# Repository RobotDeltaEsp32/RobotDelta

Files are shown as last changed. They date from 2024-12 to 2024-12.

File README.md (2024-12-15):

# RobotDelta
Este repositorio contiene el diseño y documentación completa de un robot delta desarrollado en un proyecto académico. Se realizaron cálculos de cinemática directa e inversa, simulaciones estructurales y análisis del espacio de trabajo. El control se implementó con ESP32, capturando posiciones angulares y validando con pruebas experimentales.

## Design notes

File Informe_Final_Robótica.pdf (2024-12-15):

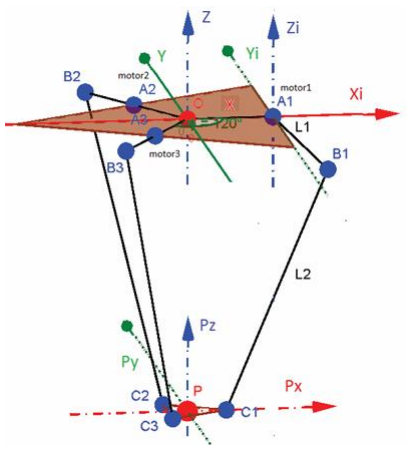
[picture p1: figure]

### Departamento de Ingeniería Mecatrónica Robótica (IMT-342) / Informe Final @ 2024 Universidad Católica Boliviana “San Pablo” – Santa Cruz

# Diseño de Robot Delta

Roberto Carlos Escobar Salcedo 8vo Semestre
roberto.escobar@ucb.edu.bo

Resumen — Este proyecto presenta el diseño, construcción y control de un robot delta, en el cual se llevaron a cabo cálculos de cinemática directa e inversa para determinar posiciones y ángulos articulares. Se realizaron simulaciones estructurales, incluyendo análisis de tensión nodal, desplazamiento estático y deformación unitaria para evaluar el comportamiento mecánico del robot. Se realizó el análisis del espacio de trabajo de este robot y se identificaron sus rangos de movimiento. El control de este robot se realizó mediante la placa ESP32 que se encargó de la captura de datos de la posición angular de los motores y de su movimiento. El proceso incluyó el diseño estructural, la selección de materiales y componentes, y la implementación de pruebas experimentales para validar el comportamiento del sistema mediante la comparación entre valores teóricos y mediciones de los valores reales.

Palabras clave: Robot delta, SCP32, Cinemática inversa, Cinemática directa, servomotores.

Abstract — This project presents the design, construction and control of a delta robot, in which forward and inverse kinematics calculations were carried out to determine joint positions and angles. Structural simulations were performed, including nodal stress analysis, static displacement and unitary deformation to evaluate the mechanical behavior of the robot. The workspace of this robot was analyzed, and its ranges of motion were identified. The control of this robot was carried out by the ESP32 board that was responsible for capturing data on the angular position of the motors and their movement. The process included the structural design, the selection of materials and components, and the implementation of experimental tests to validate the behavior of the system by comparing theoretical values with measurements of the real values.
I. INTRODUCCIÓN

La robótica ha avanzado considerablemente en los últimos años, impulsada por la necesidad de optimizar procesos en industrias que requieren rapidez, precisión y eficiencia. En este contexto, los robots delta han emergido como una solución ideal en tareas de alta velocidad y precisión, especialmente en industrias como la alimentaria, farmacéutica y electrónica, donde el manejo de objetos ligeros es crucial. Diseñado inicialmente por el Dr. Reymond Clavel, el robot delta se distingue por su arquitectura paralela, la cual permite una manipulación rápida y precisa de objetos, minimizando la inercia debido a su diseño liviano y simplificado [1].

Los robots delta utilizan tres brazos articulados que convergen en una plataforma móvil, lo que les permite alcanzar velocidades y aceleraciones superiores a las de robots con arquitecturas seriales. Este diseño ofrece además una ventaja significativa en cuanto a rigidez y precisión, lo que facilita aplicaciones de manipulación en las que se requieren altos niveles de repetibilidad [2]. Estas características han impulsado el uso de los robots delta en el ámbito industrial y en la investigación, donde la tendencia actual es integrar sensores avanzados y sistemas de visión para mejorar la precisión en entornos complejos [3].

Con lo mencionado líneas arriba este proyecto plantea el desarrollo de un robot delta para esto de debe: Obtener la cinemática directa e inversa del robot delta, realizar el dimensionamiento de los motores, diseñar la estructura en SolidWorks y comprobar funcionamiento del robot.

II. GEOMETRIA DEL ROBOT

El sistema de coordenadas inercial del robot delta se encuentra en un punto O en la base donde están ubicados los tres motores. El eje Z de este sistema de coordenadas es perpendicular a la base y el eje X perpendicular al eje del motor número 1.

Figura 1. Representación geométrica del robot delta

Sebastian Osorio Ferrufino 8vo Semestre
sebastian.osorio@ucb.edu.bo

Matías adorno Mazocato
8vo Semestre
matias.adorno@ucb.edu.bo

Jose Jesus Cabrera Pantoja Robótica IMT-342
Departamento ingeniería mecatrónica

En la Figura 1 se puede observar que cada motor tiene un brazo móvil conformado por dos eslabones, cuyas distancias son L1 y L2, las cuales son las mismas para cada brazo de cada motor. Cada motor se une al eslabón L1 por medio de una unión Ai, siendo un valor de i por cada motor (i=1, 2, 3). Los eslabones L1 y L2 se conectan mediante una unión Bi, y el eslabón L2 se une con una base móvil cuyo punto medio es el efector final P, esta unión de L2 con P se representa como Ci.

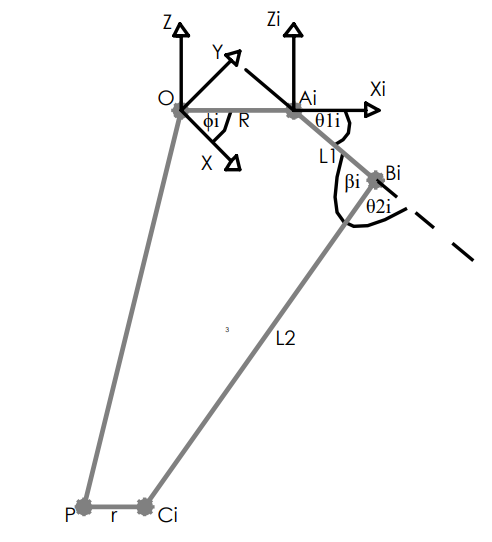
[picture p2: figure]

Figura 2. Sistemas de coordenadas y ángulos del robot delta

Cada brazo se encuentra sobre un sistema de coordenadas distinto al sistema de coordenadas inercial en el punto O, estos sistemas de coordenadas se encuentran a una distancia R con respecto al sistema de coordenadas inercial y con una rotación de un ángulo ϕi, siendo este 0°, 120° y 240° para los motores 1, 2 y 3 respectivamente, debido a que se debe tener una separación angular igual entre cada motor. Se tiene un ángulo θ1i entre el eje Xi y el vector ABi

̅̅̅, el cual es el ángulo que giran los motores, y otor ángulo θ1i entre la proyección del vector ABi

̅̅̅
y el eslabón L2. De igual manera, se tiene un ángulo interno β1i entre los eslabones L1 y L2.

Para conocer los vectores generados entre el punto inicial O y cada punto de unión se utiliza el método de la matriz de transformación, el cual representa la orientación y posición de un sistema de coordenadas rotado y trasladado respecto a otro.

OAi

̅̅̅̅̅ = [

C∅i | −S∅i | 0 RC∅i
S∅i | C∅i | 0 RS∅i
0 | 0 | 1 | 0
0 | 0 | 0 | 1

] [

0
0

0/1] = [

RC∅i
RS∅i
0
1

] Ec. 1

OBi

̅̅̅̅ = [

C∅i | −S∅i | 0 RC∅i
S∅i | C∅i | 0 RS∅i
0 | 0 | 1 | 0
0 | 0 | 0 | 1

] [

L1Cθ1i
0
−L1Sθ1i
1

] = [

C∅i

(L1Cθ1i + R)
S∅i

(L1Cθ1i + R)
−L1Sθ1i
1

] Ec. 2

OCi

̅̅̅ = [

C∅i | −S∅i | 0 RC∅i
S∅i | C∅i | 0 RS∅i
0 | 0 | 1 | 0
0 | 0 | 0 | 1

] [

PxC∅i + PyS∅i + r − R
PyC∅i − PxS∅i
Pz
1

] = [

Px + rC∅i
Py + rS∅i
Pz
1

] Ec. 3

Con las ecuaciones 1, 2 y 3 se obtienen los vectores BAi

̅̅̅̅̅,
BCi

̅̅ y ACi

̅̅.

BAi

̅̅̅̅̅ = OAi

̅̅̅̅̅ − OBi

̅̅̅̅̅ = [

−C∅iL1Cθ1i
−C∅iL1Cθ1i
L1Sθ1i
] | Ec. 4

BCi

̅̅ = OCi

̅̅̅̅ − OBi

̅̅̅̅̅ = [
Px − C∅i

(R + L1Cθ1i − r)
Py − S∅i

(R + L1Cθ1i − r)
Pz + L1Sθ1i

] Ec. 5

ACi

̅̅ = OCi

̅̅̅̅ − OAi

̅̅̅̅̅ = [
Px − C∅i

(r − R)
Py − S∅i

(r − R)
Pz

] Ec. 6

III. CINEMATICA INVERSA

La cinemática inversa permite encontrar los ángulos de entrada θ1i de cada motor a partir de conocer la posición P del efector final. Para esto se puede observar al robot de la siguiente manera:

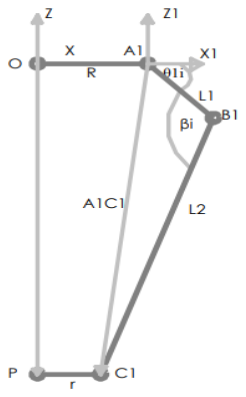
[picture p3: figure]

Figura 3. Representación trigonométrica del robot delta

En la Figura 3 se puede observar que se forma un triángulo entres los puntos Ai, Bi y Ci y se aplica teorema de cosenos para hallar la longitud de ACi

̅̅.

AC1

2 = L1

2 + L2

2 − 2L1L2 cos(βi
) | Ec. 7

Se calcula el coseno del ángulo utilizando la ecuación del producto escalar:

BAi

̅̅̅̅̅ ∗ BCi

̅̅ = |BA|
i

|BC|
i cos(βi
) | Ec. 8

Dado que L1 es la unión de los puntos A y B, y de igual manera, L2 es la unión de los puntos B y C, se tiene que:
L1 = |BA|
i | Ec. 9

L2 = |BC|
i | Ec. 10

Se reemplazan las ecuaciones 9 y 10 en la ecuación 8 y se obtiene:

cos(βi

) =

BAi

̅̅̅̅̅ ∗ BCi

̅̅
L1L2

Ec. 11

Se reemplaza la ecuación 11 en la ecuación 7:

AC1

2 = L1

2 + L2

2 − 2(BAi

̅̅̅̅̅ ∗ BCi

̅̅) | Ec. 12

Reemplazando los valores de las ecuaciones 5 y 4 en la ecuación 12:

AC1

2 = L1

2 − L2

2 + 2L1Cθ1i(PxC∅i + PyS∅i + r − R) − 2L1Sθ1iPz Ec. 13

Se tiene que la magnitud del vector ACi

̅̅ según la ecuación
6 es:

|AC|1 = AC1

2 = (Px + C∅i
(r − R))

2
+ (Py + S∅i

(r − R))

2
+ Pz … Ec. 14

Igualando las ecuaciones 13 y 14 se obtiene:

aiSθ1i + biCθ1i = ci | Ec. 15

Donde:

ai = −2PzL1 | Ec. 16
bi = 2L1(PxC∅i + PyS∅i + r − R) | Ec. 17

ci = (Px + C∅i

(r − R))

2
+ (Py + S∅i

(r − R))

2
+ Pz

2 + L1

2L2

2 Ec. 18

Utilizando identidades trigonométricas en la ecuación 15 se obtiene:

aiSθ1i + biCθ1i = √ai
2 + bi

2

∗ sin (θ1i + tan⁻¹ (

bi
ai

)) Ec. 19

Se igualan las ecuaciones 15 y 19, y se procede a despejar el ángulo de rotación de los motores:

θ1i = sin⁻¹
(

ci
√ai
2 + bi

2

)

− tan⁻¹ (

bi
ai

) Ec. 20

IV. CINEMATICA DIRECTA

La cinemática directa permite encontrar la posición P del efector final a partir del conocimiento de los ángulos de la posición de los motores.

A partir de la ecuación 5, que representa el punto de conexión del brazo con el efector final, se tiene que su magnitud es igual a L2, por lo cual se tiene que:

|BC|
i = L2

2 = (Px − C∅i
(R + L1Cθ1i − r))

2
+
(Py − S∅i

(R + L1Cθ1i − r))

2
+ (Pz + L1 + Sθ1i

)

2 Ec. 21

A partir de la ecuación 21 se realiza un sistema de ecuaciones reemplazando las 3 posiciones angulares de ϕi por cada motor, siendo estas 0°, 120° y 240° para los motores 1, 2 y 3 respectivamente.

{

(Px − R − L1cCθ11 + r)

2 + Py

2 + (Pzz + L11Sθ11)

2 = L2

2

(Px +
1
2

(R + L1Cθ12 − r))

2

+ (Py −
√3
2

(R + L1Cθ12 − r))

2
+ (Pz + L1Sθ12)

2 = L2

2

(Px +
1
2

(R + L1Cθ13 − r))

2

+ (PY +
√3
2

(R + L1Cθ13 − r))

2
+ (Pz + L1Sθ13)

2 = L2

2

Ec. 22

V. ESPACIO DE TRABAJO

El espacio de trabajo de un robot define la región tridimensional donde su efector final puede operar, teniendo en cuenta las limitaciones mecánicas, cinemáticas y estructurales. Para un robot delta, este espacio está influenciado por la geometría de los brazos, las restricciones de los actuadores y el rango angular de las articulaciones. Además, dentro de este espacio general, se encuentra el espacio de trabajo efectivo, que representa la región donde el robot puede operar de manera óptima y segura. Evaluar estas regiones es crucial para determinar la capacidad y alcance del robot en tareas específicas.

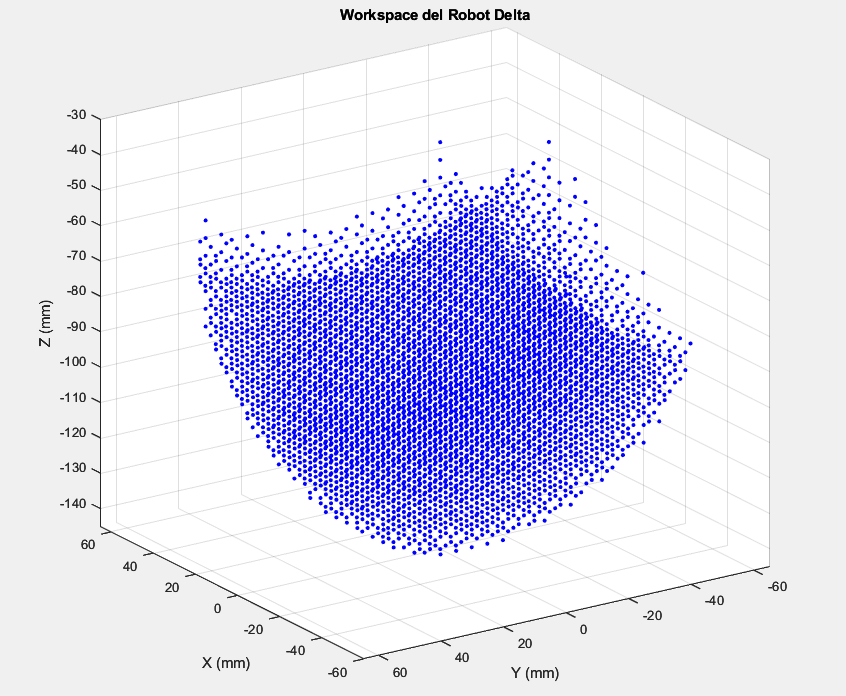
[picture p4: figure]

Figura 4. Espacio de trabajo robot delta.

Esta figura muestra el espacio de trabajo total del robot delta, representado como un conjunto de puntos en un sistema tridimensional. Cada punto corresponde a una posición alcanzable por el efector final del robot, considerando todas las configuraciones posibles. La forma generada refleja las restricciones geométricas y mecánicas del sistema, destacando las áreas donde el robot tiene mayor accesibilidad.

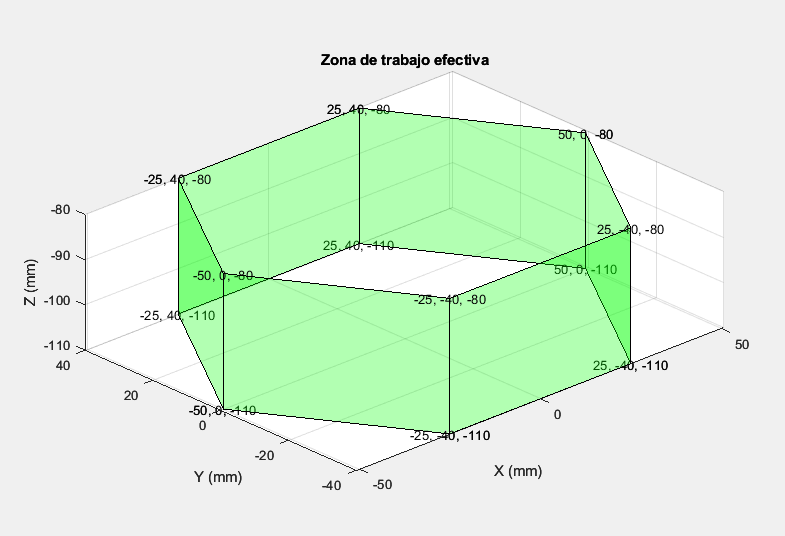
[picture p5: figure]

Figura 5. Espacio de trabajo efectivo robot delta

Aquí se representa el espacio de trabajo efectivo, una subregión dentro del espacio total donde el robot puede operar de forma segura y eficiente. Esta región está delimitada por factores como límites de velocidad, carga y precisión requerida. La figura utiliza una superficie verde para identificar claramente esta zona, resaltando las posiciones útiles y prácticas del efector final.

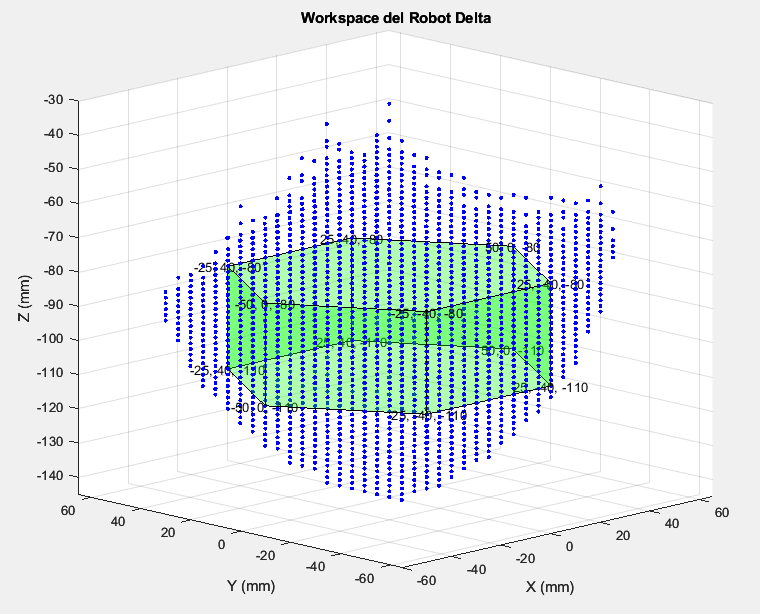
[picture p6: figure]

Figura 6. Espacio de trabajo efectivo en el espacio de trabajo total.

En esta figura se superpone el espacio de trabajo efectivo (en verde) dentro del espacio de trabajo completo (en azul). Esta representación combinada permite visualizar la relación entre ambas regiones, mostrando cómo el espacio efectivo ocupa solo una porción del espacio total. Esto es útil para identificar posibles áreas de operación óptima y para ajustar las tareas del robot a sus capacidades reales.

VI. REQUERIMIENTOS

Se presenta una tabla que muestra los requerimientos que debe cumplir el robot delta que se ha diseñado. Estos requerimientos se obtuvieron mediante el análisis de las especificaciones técnicas de los motores paso a paso utilizados, del análisis estructural y del cálculo del espacio de trabajo.

Tabla 1. Requerimientos

Requerimientos | Valores
Velocidad máxima | 300 RPM
Rango de movimiento motores | 0 a 90°
Carga máxima | 750g

VII. DISEÑO DE LA ESTRUCTURA

El proceso de diseño de la estructura del robot delta se desarrolló de manera iterativa, comenzando con la base superior, la cual se definió con una geometría triangular y lados redondeados, asegurando un soporte adecuado para los motores y los brazos. Posteriormente, se diseñó la base intermedia, con cortes rectangulares en los vértices para permitir el encaje con las patas y garantizar estabilidad. Las patas fueron diseñadas en MDF de 3 mm de grosor, con una longitud de 200 mm y segillas de 10 mm en los extremos, facilitando un ensamblaje firme con la base intermedia. Finalmente, se integraron componentes como el efector final, los brazos y los eslabones, fabricados en PLA mediante impresión 3D, asegurando precisión en las articulaciones y funcionalidad en el movimiento del robot.

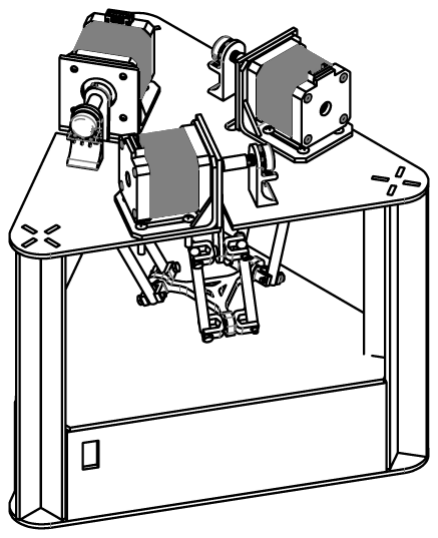
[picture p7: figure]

Figura 7. Robot delta

El criterio principal para el diseño fue la optimización de materiales y la facilidad de manufactura, utilizando MDF y PLA debido a su disponibilidad y facilidad de corte o impresión. Además, se priorizó la estabilidad estructural y el ensamblaje eficiente, garantizando que todas las piezas encajaran de forma precisa para soportar los esfuerzos durante la operación. Las dimensiones y detalles específicos, como las perforaciones para motores y las ranuras de encaje, se ajustaron para cumplir con los requisitos de funcionalidad y precisión del robot delta.

Los criterios de selección y diseño de piezas se han basado en tres factores principales: disponibilidad, costos y tiempos. La disponibilidad ha sido el criterio más importante, ya que representa la capacidad de acceder a cada componente de manera oportuna para evitar retrasos en el ensamblaje. Los costos también se han considerado cuidadosamente para mantener el proyecto dentro del presupuesto asignado, sin comprometer la funcionalidad y resistencia del robot. Además, los tiempos de armado y fabricación han sido cruciales debido a la restricción temporal del proyecto, buscando métodos de fabricación rápidos para la mayoría de las piezas y reservando métodos más complejos para los componentes que lo requieran específicamente. Estos criterios han sido clave para lograr un diseño efectivo y funcional, adaptado tanto al presupuesto como a la restricción temporal del proyecto.

VIII. SIMULACION DE ESFUERZOS

La simulación de esfuerzos es una herramienta fundamental en el diseño de sistemas mecánicos, ya que permite evaluar cómo se comportan los componentes bajo diversas condiciones de carga. A través de este análisis, es posible identificar zonas críticas de tensión, desplazamiento y deformación, garantizando así la fiabilidad y seguridad del diseño. En este caso, se realizó un análisis estático del robot delta, enfocándose en los brazos y los componentes principales, para evaluar su comportamiento estructural.

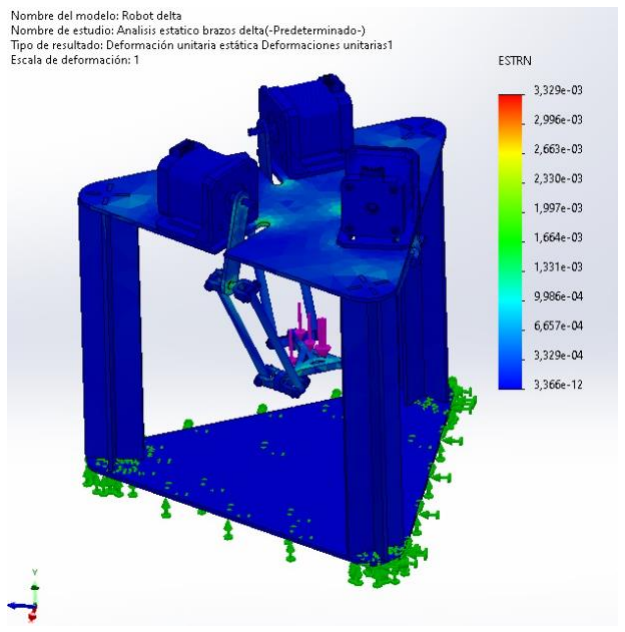
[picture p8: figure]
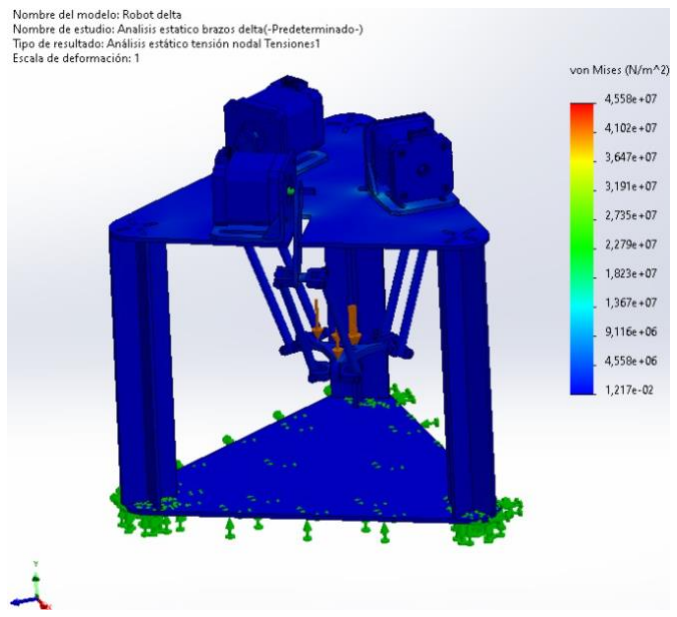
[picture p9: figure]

Figura 8. Simulación tensión nodal.

Esta simulación muestra la distribución de tensiones von Mises en el robot delta bajo una carga específica. Los colores representan los niveles de tensión, desde azul (baja tensión) hasta rojo (alta tensión). Las zonas más críticas se identifican en las áreas rojas, donde el material podría estar más cerca de su límite elástico. Esto permite evaluar la resistencia de los materiales en las partes más exigidas.

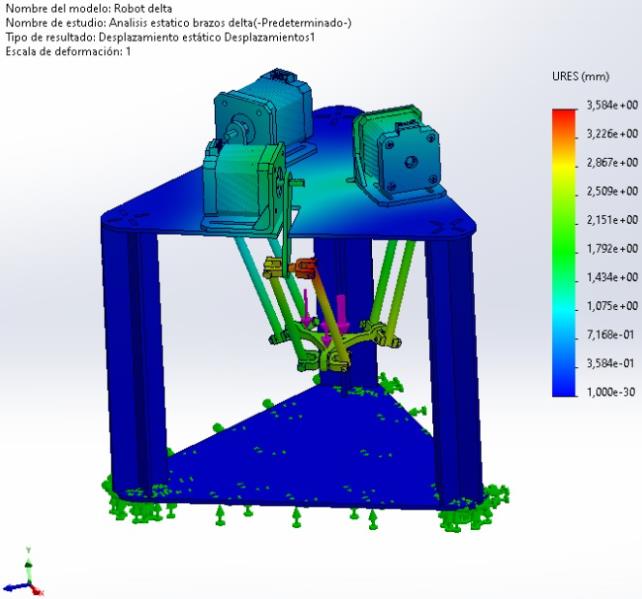
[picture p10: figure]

Figura 9. Simulación desplazamiento estático.

En este análisis, se presenta el desplazamiento total en cada nodo del robot delta. Los colores van desde azul (mínimo desplazamiento) hasta rojo (máximo desplazamiento). Este resultado es clave para entender cómo las fuerzas aplicadas afectan la estabilidad y precisión del sistema, ya que
desplazamientos | excesivos | pueden | comprometer | el
rendimiento del robot.

Figura 10. Simulación deformación unitaria estática.

La simulación muestra la deformación unitaria de los componentes del robot delta. Los colores indican la magnitud de la deformación, desde azul (mínima deformación) hasta rojo (máxima deformación). Este análisis permite verificar si las deformaciones son aceptables dentro de los límites de diseño, garantizando que no se produzcan fallos por deformación excesiva.
IX. SELECCIÓN DE MATERIALES Y COMPONENTES
A. Motor

Se ha seleccionado el motor NEMA 16, un motor paso a paso, debido a su capacidad para controlar con precisión los ángulos de los brazos del robot, lo cual es crucial para el movimiento del efector final. Este motor cuenta con un torque máximo de 1.2 kg·cm, lo que se ha evaluado como suficiente para soportar la carga requerida de 2 kg, considerando la distribución del esfuerzo entre los tres motores y la geometría del sistema. Con una longitud de eslabón de 6 cm, la fuerza máxima que cada motor puede generar se ha calculado como F =

T
d

=

1.2kg⋅cm
6cm

, resultando en una capacidad de carga de aproximadamente 0.2 kg por motor a esa distancia. Al estar distribuidos los 0.5 kg entre los tres motores, cada uno soporta una carga de aproximadamente 0.2 kg, lo que se encuentra dentro de su capacidad operativa.

Esta selección también se ha fundamentado en la disponibilidad del motor como recurso proporcionado por la universidad, lo que ha permitido su integración sin costos adicionales ni retrasos en la adquisición. Además, la naturaleza precisa y controlable de los motores NEMA 16 ha sido ideal para garantizar la estabilidad y el desempeño del efector final, validando su inclusión como componente clave en el diseño del robot delta.

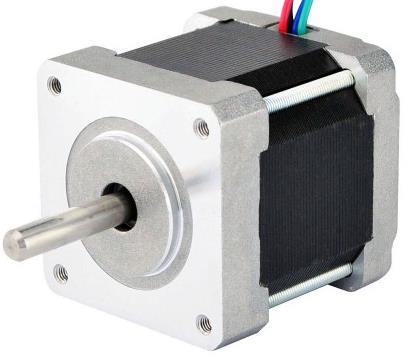
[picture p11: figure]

Figura 11. Nema 17.

B. Base del motor

Se ha decidido utilizar una base en forma de "L" para el motor NEMA 17, con el propósito de reducir los tiempos de fabricación, evitando el proceso de impresión de una base personalizada. La forma en "L" ha permitido fijar el motor de manera estable sobre la cara superior de la base estructural, asegurando una alineación adecuada en el montaje. Aunque la base específica para el NEMA 16 no se encontraba disponible, se optó por la del NEMA 17 debido a que, a pesar de ser ligeramente más grande, comparte el mismo tamaño y posición de tornillos, permitiendo su compatibilidad sin afectar la estabilidad o funcionalidad del sistema.

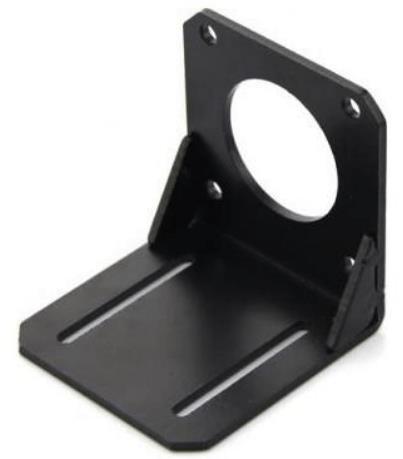
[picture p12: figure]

Figura 12. Base del motor Nema 17.

X. DISEÑO DE ESTRUCTURA
A. Base superior

El diseño de la base superior se ha realizado en una estructura triangular con lados redondeados, con una distancia de 85 mm desde el centro hasta cada arista y bordes con un radio de 20 mm. Cada cara cuenta con un corte central de 4 mm de grosor y 50 mm de longitud, terminando en un redondeado de 4 mm de radio. En cada vértice se han integrado ranuras rectangulares de 3 mm por 10 mm para fijar las patas, organizadas en forma de cruz con una separación de 10 mm entre las ranuras colineales y orientadas hacia el centro. La pieza, con un grosor uniforme de 3 mm, ha sido cortada a partir de una lámina de madera mediante una cortadora láser, logrando bordes precisos y uniformes. Este diseño ha proporcionado una base estable y alineada, con perforaciones para los motores y aperturas que garantizan el movimiento sin obstrucciones de los brazos del robot, asegurando la funcionalidad y precisión del sistema.

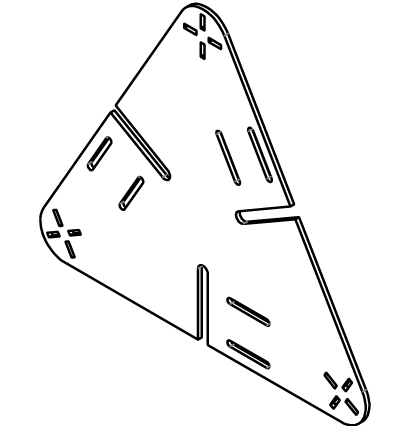
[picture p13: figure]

Figura 13. Base superior

B. Base intermedia

El diseño de la base intermedia se ha realizado en una estructura triangular con esquinas adaptadas para incluir cortes rectangulares perpendiculares de 4 mm por 10 mm. Estos cortes están diseñados para encajar perfectamente con las patas del robot, proporcionando soporte estructural adicional. A diferencia de la base superior, esta pieza no incluye esquinas redondeadas ni perforaciones para motores, enfocándose en su función como piso para el robot, colocándose sobre la parte superior de la circuitería. La base intermedia tiene una distancia de 85 mm desde el centro hasta cada arista y un grosor uniforme de 3 mm. Ha sido cortada a partir de una lámina de madera utilizando una cortadora láser, logrando una estructura precisa y estable que asegura el soporte

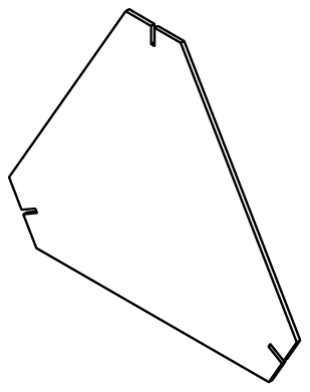
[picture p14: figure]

Figura 14. Base intermedia

C. Base inferior

El diseño de la base inferior se ha realizado en una estructura triangular con lados redondeados, con una distancia de 85 mm desde el centro hasta cada arista y bordes con un radio de 20 mm. A diferencia de la base superior, esta pieza no cuenta con cortes en las aristas ni perforaciones específicas para la fijación de motores. Sin embargo, conserva la forma triangular y un grosor uniforme de 3 mm, lo que asegura estabilidad y rigidez en la estructura general del robot. La base intermedia ha sido cortada a partir de una lámina de madera utilizando una cortadora láser, logrando bordes precisos y uniformes. Este diseño ha proporcionado soporte adicional a la estructura, mejorando su alineación y robustez para garantizar un funcionamiento óptimo del robot

Figura 14. Base inferior

C. Brazo

El brazo se ha construido en MDF de 3 mm de grosor y presenta una estructura también triangular, manteniendo una distribución uniforme de la carga en el movimiento. En el extremo destinado al motor, se ha diseñado una apertura especial que encaja con el eje, permitiendo la transmisión directa del movimiento. En el otro extremo, se ha integrado una apertura circular para el eje de la junta universal, asegurando un rango de movimiento adecuado. La distancia entre ambas aperturas es de 90 mm, y el ancho del brazo se ha definido en 15 mm, logrando así una estructura ligera y estable. Este diseño ha sido fundamental para asegurar que el brazo funcione en conjunto con el sistema, manteniendo precisión y estabilidad en cada movimiento.

Figura 15. Brazo

D. Paralelogramo

El diseño del paralelogramo se ha basado en el uso de pares de varillas de hierro liso de 5 mm de diámetro y 100 mm de longitud, seleccionadas por su rigidez y capacidad de mantener la estabilidad estructural del robot. Para proporcionar la movilidad necesaria en las articulaciones, se han realizado perforaciones tangenciales de 3 mm de diámetro a 3 mm de cada extremo de las varillas. Estas perforaciones permiten la inserción de ejes, garantizando que las varillas se conecten de forma articulada y mantengan una orientación constante del efector final durante el movimiento. Este diseño ha sido esencial para asegurar la precisión y fiabilidad del robot en tareas que requieren un control exacto de la posición y orientación.

Figura 16. Varilla

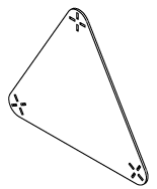
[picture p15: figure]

E. Junta universal

El diseño de la junta universal se ha compuesto por dos medias juntas impresas en 3D, las cuales presentan una estructura simétrica. Cada media junta incluye un eje circular con un corte cuadrado tangencial en su base, lo que permite que ambas piezas puedan unirse de manera precisa al voltear una de ellas y pegarla a la otra utilizando cianoacrilato en la zona de corte. Después del eje circular, la pieza se extiende en una forma de “U” con ángulos rectos y una perforación circular de 3 mm en cada lado. Esta perforación permite la inserción de un eje que conecta la junta universal a la varilla del robot. La estructura del eje central proporciona rotación en el eje y, mientras que la perforación y su eje permiten rotación en el eje x, otorgando así un rango de movimiento multidireccional al sistema. Este diseño ha sido esencial para proporcionar flexibilidad y precisión en los movimientos del efector final.

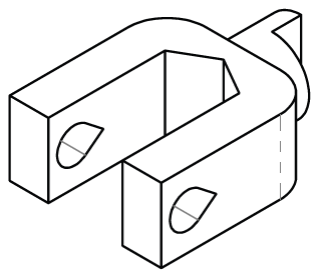
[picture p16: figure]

Figura 17. Medio eje universal.

F. Efector final

El efector final tiene una forma en “Y”, con ángulos de 120 grados entre cada uno de sus brazos, lo que permite una distribución simétrica ideal para controlar de manera precisa el movimiento. Cada brazo tiene una longitud de 35 mm medida desde el centro hasta el centro de los orificios, un ancho de 5 mm y un grosor de 5 mm, proporcionando una estructura ligera pero robusta. En los extremos de cada brazo se encuentran perforaciones diseñadas específicamente para conectar juntas universales, asegurando el rango de movimiento necesario para adaptarse a las orientaciones y posiciones requeridas por el robot. Este componente ha sido fabricado en material PLA mediante impresión 3D, lo que ha permitido obtener un diseño preciso y funcional. Su estructura ha sido clave para garantizar la estabilidad y precisión del efector final en las tareas asignadas.

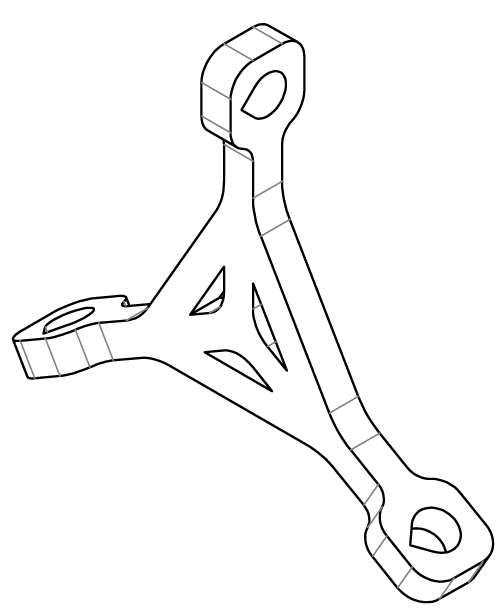
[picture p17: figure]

Figura 18. Efector final

G. Soporte

Los soportes del robot han sido fabricados en MDF con un grosor de 3 mm, proporcionando rigidez estructural y estabilidad al diseño. Cada pata tiene una longitud de 200 mm, excluyendo las rejillas que se encuentran en cada extremo. Estas rejillas, diseñadas para facilitar el encaje y soporte en la estructura, tienen un largo de 10 mm cada una y están separadas entre sí por una distancia de 10 mm. La pata presenta un ancho total de 40 mm, lo que asegura una base sólida y resistente para soportar el peso y las dinámicas del robot durante su operación. Este diseño ha sido clave para garantizar una conexión estable con el resto de la estructura y para mantener la alineación adecuada del sistema.

Figura 19. Soporte

H. Seguidor del eslabón

El seguidor es una pieza fabricada en PLA mediante impresión 3D, diseñada para ajustar y fijar el eslabón en el sistema del robot delta. Tiene una forma semicircular con un diámetro externo de 8.10 mm y un radio interno de 2 mm, con una altura total de 10.93 mm y un grosor de base de 2 mm, y un grosor de la lengüeta de 3mm equivalente al grosor del eslabón. En su parte superior, cuenta con un corte plano de 4.10 mm en la sección interna para asegurar un encaje preciso con el eslabón, mientras que su orificio central, con un diámetro de 3.07 mm, está diseñado para alojar un eje que permite un movimiento articulado. Además, la base del seguidor incluye una extensión de 4.30 mm que facilita su integración con otros componentes del robot. Este diseño compacto y funcional garantiza la estabilidad y precisión del eslabón, contribuyendo al correcto desempeño del sistema en tareas asignadas.

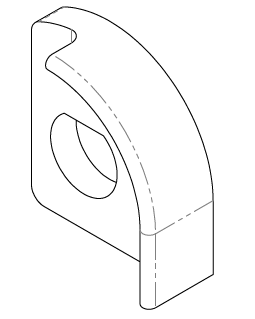
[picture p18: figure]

Figura 20. Seguidor de eslabón

I. Base de potenciómetro

La base del potenciómetro, fabricada en PLA mediante impresión 3D, tiene una altura total de 38.5 mm y un diseño optimizado para sostener el potenciómetro de manera precisa. Cuenta con un orificio central de 6.76 mm de diámetro ubicado a 29 mm desde la base, mientras que su parte superior incluye un redondeo con un radio de 9.5 mm para facilitar el montaje. En la parte trasera, posee dos brazos laterales de 2 mm de grosor y 9 mm de longitud, situados a una altura de 17.12 mm desde la base principal, proporcionando soporte adicional. La base inferior, con una longitud de 13 mm, garantiza la estabilidad estructural y permite una fijación firme al sistema. Este diseño asegura que el potenciómetro se mantenga alineado y funcional dentro del conjunto del robot delta.

Figura 21. Base del potenciómetro

X. PRUEBAS EXPERIMENTALES

En esta sección se describen las pruebas experimentales realizadas para evaluar el desempeño del sistema de control del robot, comparando los valores teóricos de los ángulos articulares (q) obtenidos a partir de modelos matemáticos, con los valores medidos por los sensores (potenciómetros).

Se realizó un análisis experimental para encontrar la resolución de los potenciómetros en la cual se utilizó una placa ESP32 para su alimentación y lectura, la cual tiene 12 bits de resolución, es decir, que realiza lecturas analógicas de 0 a 3,3V representándolas en un rango de 0 a 4095. En dicho análisis se obtuvieron los siguientes rangos:

Potenciómetro 1 (s1): 1790 a 3200, donde 1790 es igual a una posición angular de 90° del motor 1 y 3200 es igual a 0°.

Potenciómetro 2 (s2): 1810 a 3160, donde 1810 es igual a una posición angular de 90° del motor 2 y 3160 es igual a 0°.

Potenciómetro 3 (s3): 2000 a 3160, donde 2000 es igual a una posición angular de 90° del motor 3 y 3160 es igual a 0°.

La diferencia entre los valores teóricos y los medidos permite calcular el error para cada articulación, lo que se presenta en gráficos de barras. Por otro lado, los gráficos de líneas muestran una comparación directa entre los ángulos teóricos (q) y los valores reales obtenidos de los potenciómetros.

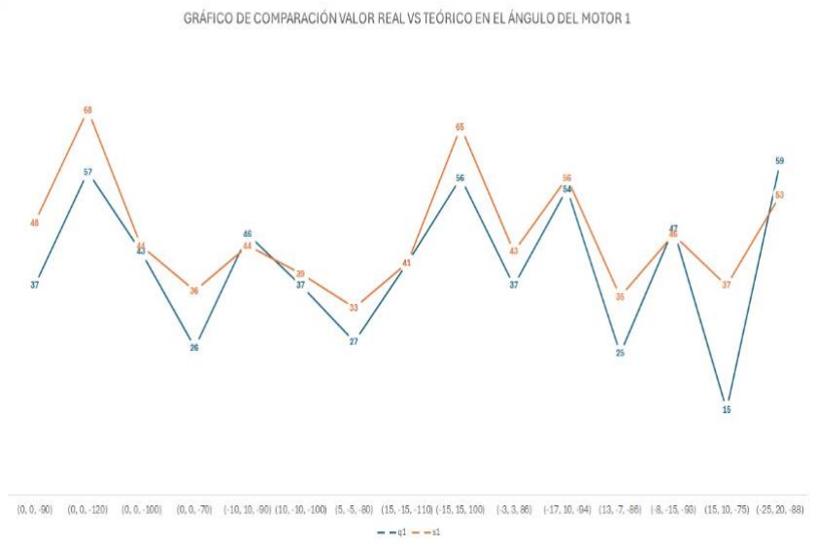
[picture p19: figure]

Figura 22. Gráfico comparativo entre q1 y s1.

La Figura 22 compara el ángulo teórico q1 (Línea azul) con el valor medido s1 (Línea naranja) del potenciómetro correspondiente al motor 1. Las líneas muestran cómo se comportan los valores teóricos y medidos a lo largo del tiempo o del rango de movimiento.

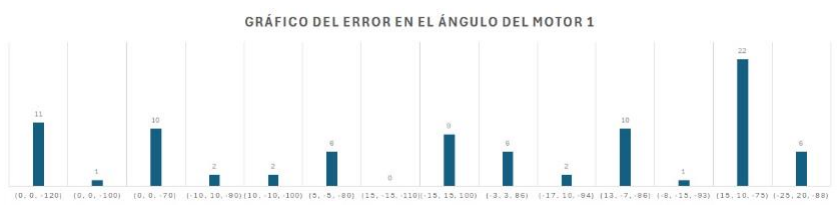
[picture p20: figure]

Figura 23. Gráfico del error del motor 1.

La Figura 23 presenta el error absoluto del motor 1. El error se calcula como la diferencia entre el valor teórico q1 y el valor medido por el potenciómetro s1. Las barras muestran la magnitud del error en distintas posiciones del motor.

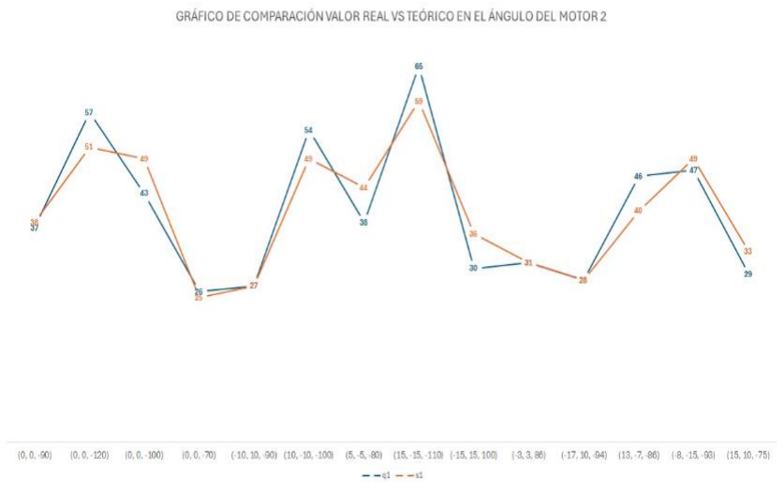
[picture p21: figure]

Figura 24. Gráfico comparativo entre q2 y s2.

La Figura 24 representa la comparación entre el ángulo teórico q2 (Línea azul) y el valor obtenido de s2 (Línea naranja). Las líneas permiten observar posibles discrepancias entre ambos valores.

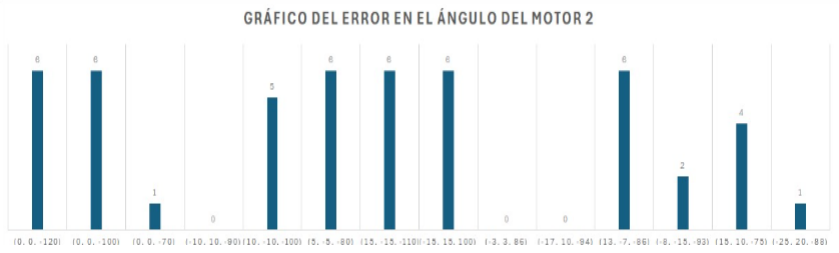
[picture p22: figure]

Figura 25. Gráfico de error del motor 2.

La Figura 25 muestra el error absoluto para el motor 2. Se representa la diferencia entre q2 (teórico) y s2 (medido por el potenciómetro). Se puede observar que se tiene una repetición constante de un error de 6°.

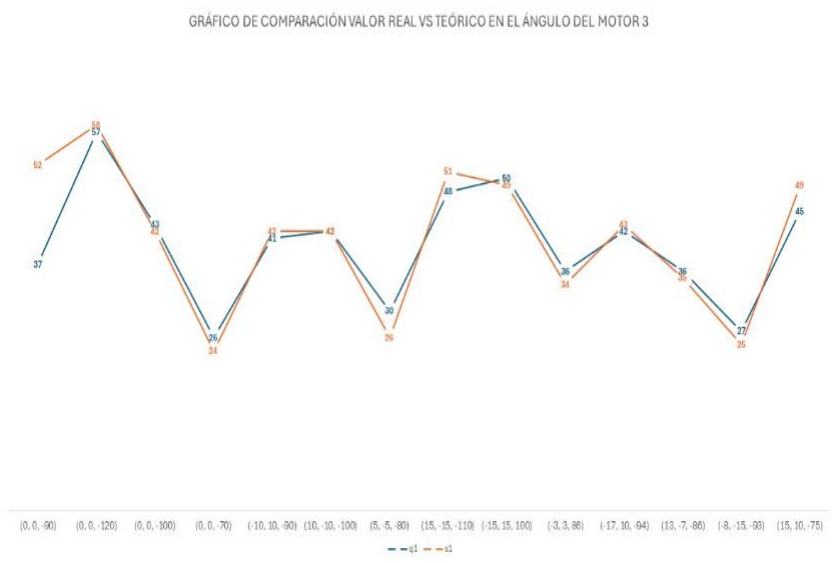
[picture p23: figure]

Figura 26. Gráfico comparativo entre q3 y s3.

La Figura 26 muestra la comparación entre el ángulo teórico q1 y el valor medido s3 del potenciómetro del motor 3. La similitud entre las líneas refleja la precisión del sistema de medición y control a diferencia a los gráficos de q1 y q2.

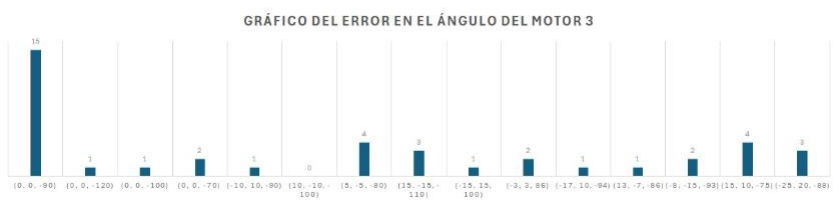
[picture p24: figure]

Figura 27. Gráfico del error del motor 3.

En la Figura 27 se visualiza el error absoluto para el motor
3. La diferencia entre q3 y s3 se presenta en forma de barras, facilitando la identificación de desviaciones en las mediciones en donde se puede observar que la primera barra es un valor mucho mayor comparado al del resto que no tiene mucha diferencia.

XI. CONCLUSIONES

En este proyecto se realizó el diseño y construcción de un robot delta para lo cual se realizaron cálculos de cinemática inversa, cinemática directa, espacio de trabajo, espacio de trabajo efectivo, diseño de la estructura en SolidWorks, con el cual se realizó la simulación de la tensión nodal, desplazamiento estático y la deformación unitaria estática sobre el robot. Para la construcción de robot se utilizaron principalmente dos materiales: PLA (ácido poliláctico) y MDF (Fibras de densidad media), la estructura y los primeros eslabones de los brazos se realizaron de mdf por otro lado los ejes, las varillas y el efector final están hechos de PLA.

Finalmente, se ejecutaron pruebas experimentales para verificar el desempeño del sistema. Se compararon los valores teóricos de los ángulos de los motores obtenidos mediante
cálculos | de | cinemática | inversa | con | las | mediciones
proporcionadas por los sensores (potenciómetros) instalados en el robot. Con estos valores se realizaron gráficos con los cuales se logró visualizar el error que este robot presentó.
XII. BIBLIOGRAFÍA
[1] R. Clavel, Conception d'un robot parallèle rapide à 4
degrés | de | liberté, | Lausanne, | Switzerland: | École
Polytechnique Fédérale de Lausanne, 1991.
[2] C. Gosselin and J. Angeles, "Singularity Analysis of Closed-Loop Kinematic Chains," IEEE Transactions on Robotics and Automation, vol. 6, no. 3, pp. 281-290, Jun. 1990.
[3] M. Honegger, H. Yoshihito, and I. Codourey, "Sensor Fusion for High-Performance Robots: The Delta Example," in Proceedings of the IEEE International Conference on Robotics and Automation (ICRA), Nagoya, Japan, 1995, pp. 1717-1722.
[4] J. Gudiño-Lau, J. Alcalá-Rodríguez, H. Narrarro, D. Velez-Díaz, y S. Charre-Ibarra, "Diseño y modelo cinemático de un robot delta para el diagnóstico y rehabilitación," Boletín Científico Tlahuelilpan, vol. 8, pp. 1-10, 2017
[5] W. C. Pachacama Oña y J. F. Salazar Muzo, Diseño y construcción de un prototipo de robot delta para aplicaciones pick & place, tesis de grado, Facultad de Ingeniería Eléctrica y Electrónica, Escuela Politécnica Nacional, Quito, Ecuador, 2016

XII. ANEXOS

A. Código para la interfaz de control del robot delta #include <WiFi.h>
#include <WiFiMulti.h>

#define paso1 15

#define dire1 2

#define paso2 13

#define dire2 12

#define paso3 25

#define dire3 26

#define sensor_1 33

#define sensor_2 35

#define sensor_3 32

int s1, s2, s3;
int grado1;
int grado2;
int grado3;
int pasos1;
int pasos2;
int pasos3;

int R = 60;
int r = 35;
int L1 = 60;
int L2 = 90;
int retardo = 2000;

WiFiMulti wifiMulti;
WiFiServer servidor(80);

String modo = "cordenadas";
float X = 0.0, Y = 0.0, Z = -90.0; float q1 = 0.0, q2 = 0.0, q3 = 0.0;

bool bandera = false;

void calculo_de_cordenadas();
void calculo_de_q();
void pasopaso();
void control();
void calculo_de_s();

void setup() {
pinMode(paso1, OUTPUT);
pinMode(dire1, OUTPUT);
pinMode(paso2, OUTPUT);
pinMode(dire2, OUTPUT);
pinMode(paso3, OUTPUT);
pinMode(dire3, OUTPUT);

Serial.begin(115200);
Serial.println("\nIniciando WiFi Multi");

//wifiMulti.addAP("mazzocato", "leon6734"); wifiMulti.addAP("MATIAS", "Emily123");

WiFi.mode(WIFI_STA);
Serial.print("Conectando a WiFi..."); while (wifiMulti.run() != WL_CONNECTED) { Serial.print(".");
delay(1000);
}
if | (WiFi.localIP() | == | INADDR_NONE | ||
WiFi.localIP().toString() == "0.0.0.0") { Serial.println("\nError: No se obtuvo una IP válida. Reiniciando...");
ESP.restart(); // Reinicia el microcontrolador
}

Serial.println("\nConectado a WiFi"); Serial.print("IP local: "); Serial.println(WiFi.localIP());
servidor.begin();
Serial.println("Servidor iniciado correctamente"); }

void loop() {
WiFiClient cliente = servidor.available();
if (cliente) {
Serial.println("Nuevo cliente conectado"); String peticion = cliente.readStringUntil('\r'); cliente.flush();
int q1Index = peticion.indexOf("q1=");
int q2Index = peticion.indexOf("q2=");
int q3Index = peticion.indexOf("q3="); int xIndex = peticion.indexOf("X=");
int yIndex = peticion.indexOf("Y=");
int zIndex = peticion.indexOf("Z=");
if (q1Index!=q1 && q2Index!=q2 && q3Index!=q3 && xIndex!=X && yIndex!=Y && zIndex!=Z){
if (peticion.indexOf("GET /modo/cordenadas") >= 0) { modo = "cordenadas";
}else if (peticion.startsWith("GET /actualizar?")) { s1 = analogRead(sensor_1);
s2 = analogRead(sensor_2);
s3 = analogRead(sensor_3);

if (q1Index >= 0) q1 = peticion.substring(q1Index + 3, peticion.indexOf('&', q1Index)).toFloat();
if (q2Index >= 0) q2 = peticion.substring(q2Index + 3, peticion.indexOf('&', q2Index)).toFloat();
if (q3Index >= 0) q3 = peticion.substring(q3Index + 3, peticion.indexOf('&', q3Index)).toFloat();
if (xIndex >= 0) X = peticion.substring(xIndex + 2, peticion.indexOf('&', xIndex)).toFloat();
if (yIndex >= 0) Y = peticion.substring(yIndex + 2, peticion.indexOf('&', yIndex)).toFloat();
if (zIndex >= 0) Z = peticion.substring(zIndex + 2, peticion.indexOf('&', zIndex)).toFloat();

bandera = false;
}
enviarPaginaWeb(cliente);
if (modo == "cordenadas") {
if (bandera == false) {
calculo_de_s(); // Calcula los valores actuales de los sensores
control();
bandera = true;
}
}
}
delay(6500);
cliente.stop();
Serial.println("Cliente desconectado"); }
}

void enviarPaginaWeb(WiFiClient &cliente) { cliente.println("HTTP/1.1 200 OK"); cliente.println("Content-Type: text/html; charset=UTF-8");
cliente.println("Connection: close"); cliente.println();

cliente.println("<!DOCTYPE HTML>"); cliente.println("<html>");

cliente.println("<head>");
cliente.println("<style>");
cliente.println("button { background-color: #4CAF50; color: white; padding: 10px; margin: 5px; }"); cliente.println("input { width: 50px; }"); cliente.println("</style>"); cliente.println("</head>"); cliente.println("<body>");

if (modo == "cordenadas") {
cliente.println("<h2>Modo: Coordenadas</h2>"); cliente.println("<form>");
cliente.println("<p>X=<input | type='text' | id='X'
value='" + String(X, 2) + "'></p>");
cliente.println("<p>Y=<input | type='text' | id='Y'
value='" + String(Y, 2) + "'></p>");
cliente.println("<p>Z=<input | type='text' | id='Z'
value='" + String(Z, 2) + "'></p>"); cliente.println("<p>q1=" + String(q1, 2) + "</p>"); cliente.println("<p>q2=" + String(q2, 2) + "</p>"); cliente.println("<p>q3=" + String(q3, 2) + "</p>"); cliente.println("</form>");
} else {
cliente.println("<h2>Error: Modo no soportado</h2>"); }
cliente.println("<button
onclick=\"actualizar()\">Actualizar</button>"); cliente.println("<script>");
cliente.println("function actualizar() {"); cliente.println(" let params = '';");
cliente.println(" | | | | if
(!document.getElementById('X').value | ||
!document.getElementById('Y').value | ||
!document.getElementById('Z').value) {"); cliente.println(" alert('Por favor, ingrese todos los valores.');");
cliente.println(" return;");
cliente.println(" }");
cliente.println(" | params | += | 'X=' | +
document.getElementById('X').value + '&';");
cliente.println(" | params | += | 'Y=' | +
document.getElementById('Y').value + '&';");
cliente.println(" | params | += | 'Z=' | +
document.getElementById('Z').value + '&';");
cliente.println(" | fetch('/actualizar?' | +
params).then(response => location.reload());"); cliente.println("}");
cliente.println("</script>");

cliente.println("</body>"); cliente.println("</html>"); }

void calculo_de_q() {
float a1 = -2*Z*L1;
float b1 = 2*L1*(X*cos(0)+Y*sin(0)+r-R);
float | c1 | = | pow(X+cos(0)*(r-R),2)+pow(Y+sin(0)*(r-
R),2)+pow(Z,2)+pow(L1,2)-pow(L2,2);

float a2 = -2*Z*L1;
float | b2 | =
2*L1*(X*cos(radians(120))+Y*sin(radians(120))+r-R);
float | c2 | = | pow(X+cos(radians(120))*(r-
R),2)+pow(Y+sin(radians(120))*(r-R),2)+pow(Z,2)+pow(L1,2)-pow(L2,2);

float a3 = -2*Z*L1;

float | b3 | =
2*L1*(X*cos(radians(240))+Y*sin(radians(240))+r-R);
float | c3 | = | pow(X+cos(radians(240))*(r-
R),2)+pow(Y+sin(radians(240))*(r-R),2)+pow(Z,2)+pow(L1,2)-pow(L2,2);
float | q1rad | = | asin(c1/sqrt(pow(a1,2)+pow(b1,2)))-
atan(b1/a1);
float | q2rad | = | asin(c2/sqrt(pow(a2,2)+pow(b2,2)))-
atan(b2/a2);
float | q3rad | = | asin(c3/sqrt(pow(a3,2)+pow(b3,2)))-
atan(b3/a3);

q1 = (int)(q1rad*(180/PI));
q2 = (int)(q2rad*(180/PI));
q3 = (int)(q3rad*(180/PI));
}

void pasopaso() {
pasos1 = floor((abs(q1-grado1)/1.8)*16);
pasos2 = floor((abs(q2-grado2)/1.8)*16);
pasos3 = floor((abs(q3-grado3)/1.8)*16);

if(q1>grado1 && q1>=0 && q1<=90 && q2>=0 && q2<=90 && q3>=0 && q3<=90){
digitalWrite(dire1, HIGH);
for(int i1=0; i1<=pasos1; i1++){
digitalWrite(paso1, HIGH); delayMicroseconds(retardo); digitalWrite(paso1, LOW);
delayMicroseconds(retardo);
}
}
if(q2>grado2 && q1>=0 && q1<=90 && q2>=0 && q2<=90 && q3>=0 && q3<=90){
digitalWrite(dire2, HIGH);
for(int i2=0; i2<=pasos2; i2++){
digitalWrite(paso2, HIGH); delayMicroseconds(retardo); digitalWrite(paso2, LOW);
delayMicroseconds(retardo);
}
}
if(q3>grado3 && q1>=0 && q1<=90 && q2>=0 && q2<=90 && q3>=0 && q3<=90){
digitalWrite(dire3, HIGH);
for(int i3=0; i3<=pasos3; i3++){
digitalWrite(paso3, HIGH); delayMicroseconds(retardo); digitalWrite(paso3, LOW);
delayMicroseconds(retardo);
}
}
if(q1<grado1 && q1>=0 && q1<=90 && q2>=0 && q2<=90 && q3>=0 && q3<=90){
digitalWrite(dire1, LOW);
for(int j1=0; j1<=pasos1; j1++){
digitalWrite(paso1, HIGH); delayMicroseconds(retardo); digitalWrite(paso1, LOW);
delayMicroseconds(retardo);
}
}
if(q2<grado2 && q1>=0 && q1<=90 && q2>=0 && q2<=90 && q3>=0 && q3<=90){
digitalWrite(dire2, LOW);
for(int j2=0; j2<=pasos2; j2++){
digitalWrite(paso2, HIGH); delayMicroseconds(retardo); digitalWrite(paso2, LOW);
delayMicroseconds(retardo); }

}
if(q3<grado3 && q1>=0 && q1<=90 && q2>=0 && q2<=90 && q3>=0 && q3<=90){
digitalWrite(dire3, LOW);
for(int j3=0; j3<=pasos3; j3++){
digitalWrite(paso3, HIGH); delayMicroseconds(retardo); digitalWrite(paso3, LOW);
delayMicroseconds(retardo); }
}
}

void calculo_de_s() {

grado1 = map(s1, 3200, 1790, 0, 90); grado2 = map(s2, 3160, 1810, 0, 90); grado3 = map(s3, 3160, 2000, 0, 90);

Serial.print("s1: "); Serial.print(grado1); Serial.print(" s2: "); Serial.print(grado2); Serial.print(" s3: "); Serial.println(grado3); }
void control() {
if (modo == "cordenadas") {
calculo_de_q();
pasopaso();
}
}

B. Código para la realización de una secuencia de movimientos del robot delta

#define paso_1 15

#define dire_1 2

#define paso_2 13

#define dire_2 12

#define paso_3 25

#define dire_3 26

#define sensor_1 33

#define sensor_2 35

#define sensor_3 32

int R = 60;
int r = 35;
int L1 = 60;
int L2 = 90;
int retardo = 2000;

int secuenciaX[4] = {-30, -30, 30, 30}; int secuenciaY[4] = {-30, 30, 30,-30};
int secuenciaZ[4] = {-90, -90,-90,-90};

void secuencia();
void cinematica(int x, int y, int z, int grado1, int grado2, int grado3);

void setup() {
pinMode(paso_1, OUTPUT); pinMode(dire_1, OUTPUT); pinMode(paso_2, OUTPUT); pinMode(dire_2, OUTPUT); pinMode(paso_3, OUTPUT); pinMode(dire_3, OUTPUT);

Serial.begin(115200);
Serial.println("Iniciando secuencia...");
}

void loop() {
secuencia();
delay(4000);
}

void secuencia() {
for (int i = 0; i < 4; i++) { int s1 = analogRead(sensor_1);
int s2 = analogRead(sensor_2);
int s3 = analogRead(sensor_3);

int grado1 = map(s1, 3200, 1790, 0, 90);
int grado2 = map(s2, 3160, 1810, 0, 90);
int grado3 = map(s3, 3160, 2000, 0, 90);

Serial.print("Ejecutando paso "); Serial.println(i + 1);
Serial.print("X: "); Serial.print(secuenciaX[i]); Serial.print(", Y: "); Serial.print(secuenciaY[i]); Serial.print(", Z: "); Serial.println(secuenciaZ[i]);

cinematica(secuenciaX[i], secuenciaY[i], secuenciaZ[i], grado1, grado2, grado3);
delay(4000);
}
}

void cinematica(int x, int y, int z, int grado1, int grado2, int grado3) {
float a1 = -2*z*L1;
float b1 = 2*L1*(x*cos(0)+y*sin(0)+r-R);
float c1 = pow(x+cos(0)*(r-R),2)+pow(y+sin(0)*(r-R),2)+pow(z,2)+pow(L1,2)-pow(L2,2);

float a2 = -2*z*L1;
float b2 =
2*L1*(x*cos(radians(120))+y*sin(radians(120))+r-R);

float c2 = pow(x+cos(radians(120))*(r-R),2)+pow(y+sin(radians(120))*(r-R),2)+pow(z,2)+pow(L1,2)-pow(L2,2);

float a3 = -2*z*L1;
float b3 =
2*L1*(x*cos(radians(240))+y*sin(radians(240))+r-R); float c3 = pow(x+cos(radians(240))*(r-R),2)+pow(y+sin(radians(240))*(r-R),2)+pow(z,2)+pow(L1,2)-pow(L2,2);

float q1rad = asin(c1/sqrt(pow(a1,2)+pow(b1,2)))-atan(b1/a1);
float q2rad = asin(c2/sqrt(pow(a2,2)+pow(b2,2)))-atan(b2/a2);
float q3rad = asin(c3/sqrt(pow(a3,2)+pow(b3,2)))-atan(b3/a3);

int q1 = q1rad*(180/PI);
int q2 = q2rad*(180/PI);
int q3 = q3rad*(180/PI);
int pasos1 = floor((abs(q1-grado1)/1.8)*16); int pasos2 = floor((abs(q2-grado2)/1.8)*16);
int pasos3 = floor((abs(q3-grado3)/1.8)*16);

Serial.print("q1: "); Serial.println(q1); Serial.print("sensor1: "); Serial.println(grado1); Serial.print("q2: "); Serial.println(q2); Serial.print("sensor2: "); Serial.println(grado2); Serial.print("q3: "); Serial.println(q3); Serial.print("sensor3: "); Serial.println(grado3); Serial.println("---------------------------------");

if(q1>grado1 && q1>=0 && q1<=90 && q2>=0 && q2<=90 && q3>=0 && q3<=90) {
digitalWrite(dire_1, HIGH);
for(int i1=0; i1<=pasos1; i1++){ digitalWrite(paso_1, HIGH); delayMicroseconds(retardo); digitalWrite(paso_1, LOW); delayMicroseconds(retardo);
}
}
if(q1<grado1 && q1>=0 && q1<=90 && q2>=0 && q2<=90 && q3>=0 && q3<=90){
digitalWrite(dire_1, LOW);
for(int j1=0; j1<=pasos1; j1++){ digitalWrite(paso_1, HIGH); delayMicroseconds(retardo); digitalWrite(paso_1, LOW); delayMicroseconds(retardo); }
}

if(q2>grado2 && q1>=0 && q1<=90 && q2>=0 && q2<=90 && q3>=0 && q3<=90){
digitalWrite(dire_2, HIGH);
for(int i2=0; i2<=pasos2; i2++) { digitalWrite(paso_2, HIGH); delayMicroseconds(retardo); digitalWrite(paso_2, LOW); delayMicroseconds(retardo);
}
}
if(q2<grado2 && q1>=0 && q1<=90 && q2>=0 && q2<=90 && q3>=0 && q3<=90){
digitalWrite(dire_2, LOW);
for(int j2=0; j2<=pasos2; j2++){ digitalWrite(paso_2, HIGH);

delayMicroseconds(retardo); digitalWrite(paso_2, LOW); delayMicroseconds(retardo);
}
}
if(q3>grado3 && q1>=0 && q1<=90 && q2>=0 && q2<=90 && q3>=0 && q3<=90){
digitalWrite(dire_3, HIGH);
for(int i3=0; i3<=pasos3; i3++){ digitalWrite(paso_3, HIGH); delayMicroseconds(retardo); digitalWrite(paso_3, LOW); delayMicroseconds(retardo);
}
}
if(q3<grado3 && q1>=0 && q1<=90 && q2>=0 && q2<=90 && q3>=0 && q3<=90){
digitalWrite(dire_3, LOW);
for(int j3=0; j3<=pasos3; j3++){ digitalWrite(paso_3, HIGH); delayMicroseconds(retardo); digitalWrite(paso_3, LOW); delayMicroseconds(retardo); }
}
}

C. Código para encontrar el espacio de trabajo del robot delta

clc;
clear;
close all;

vertices = [
-50, 0, -80;
-25,-40, -80;
25,-40, -80;
50, 0, -80;
25, 40, -80;
-25, 40, -80;
-50, 0, -110;
-25,-40, -110;
25,-40, -110;
50, 0, -110;
25, 40, -110;
-25, 40, -110;
];

faces = [
1,2,3,4,5,6;
7,8,9,10,11,12;
];
faces2 = [
1,2,8,7;
2,3,9,8;
3,4,10,9;
4,5,11,10;
5,6,12,11;
6,1,7,12;
];

figure;
hold on;

patch('Vertices', vertices, 'Faces', faces, 'Faces', faces2, ...
'FaceColor', 'green', 'FaceAlpha', 0.3, ... 'EdgeColor', 'black');

for i = 1:size(vertices, 1)
text(vertices(i, 1), vertices(i, 2), vertices(i, 3), ...
sprintf('%d, %d, %d', vertices(i, :)), ... 'FontSize', 10, 'Color', 'black', 'HorizontalAlignment', 'center');
end

xlabel('X (mm)');
ylabel('Y (mm)');
zlabel('Z (mm)');
title('Figura del Prisma Rectangular'); grid on;
axis equal;
view(3);

R = 60;
r = 35;
L1 = 60;
L2 = 90;

x_range = -250:5:250;
y_range = -200:5:200;
z_range = 0:-5:-150;

workspace_points = [];
[X, Y, Z] = meshgrid(x_range, y_range, z_range); points = [X(:), Y(:), Z(:)];

for i = 1:size(points, 1)

point = points(i, :);
[q, is_reachable] = inverse_kinematics(point, R, r, L1, L2);
if is_reachable
workspace_points = [workspace_points; point]; end
end

scatter3(workspace_points(:, 1), workspace_points(:, 2), workspace_points(:, 3), 10, 'b', 'filled');
xlabel('X (mm)');
ylabel('Y (mm)');
zlabel('Z (mm)');
title('Workspace del Robot Delta');
grid on;
axis equal;

function [q, is_reachable] = inverse_kinematics(point, R, r, L1, L2)
x = point(1);
y = point(2);
z = point(3);

a1 = -2*z*L1;
b1 = 2*L1*(x*cosd(0)+y*sind(0)+r-R); c1 = (x+cosd(0)*(r-R))^2+(y+sind(0)*(r-R))^2+(z^2)+(L1^2)-(L2^2);

a2 = -2*z*L1;
b2 = 2*L1*(x*cosd(120)+y*sind(120)+r-R); c2 = (x+cosd(120)*(r-R))^2+(y+sind(120)*(r-R))^2+(z^2)+(L1^2)-(L2^2);

a3 = -2*z*L1;
b3 = 2*L1*(x*cosd(240)+y*sind(240)+r-R); c3 = (x+cosd(240)*(r-R))^2+(y+sind(240)*(r-R))^2+(z^2)+(L1^2)-(L2^2);

try
q1 = asind(c1/sqrt((a1^2)+(b1^2)))-atand(b1/a1); q2 = asind(c2/sqrt((a2^2)+(b2^2)))-atand(b2/a2); q3 = asind(c3/sqrt((a3^2)+(b3^2)))-atand(b3/a3);

if all(q1>0 & q1<90) && ...
all(q2>0 & q2<90) && ...
all(q3>0 & q3<90)
is_reachable = true;
else
is_reachable = false;
end
q = [q1, q2, q3];
catch
q = [];
is_reachable = false;
end
end

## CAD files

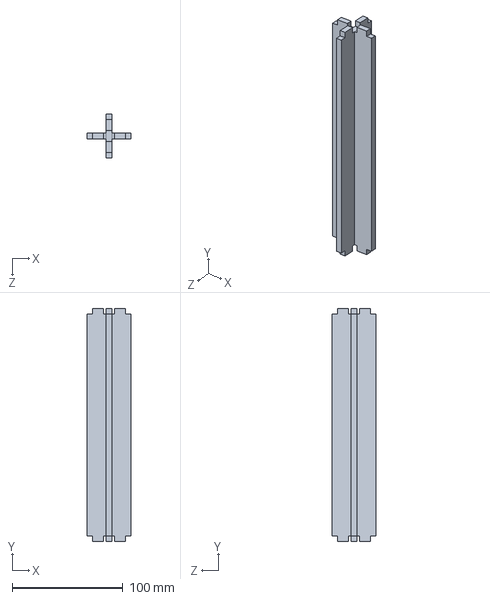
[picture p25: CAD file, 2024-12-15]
3D/Pata.SLDASM
40.0 x 210.0 x 40.0 mm
Pata x 2

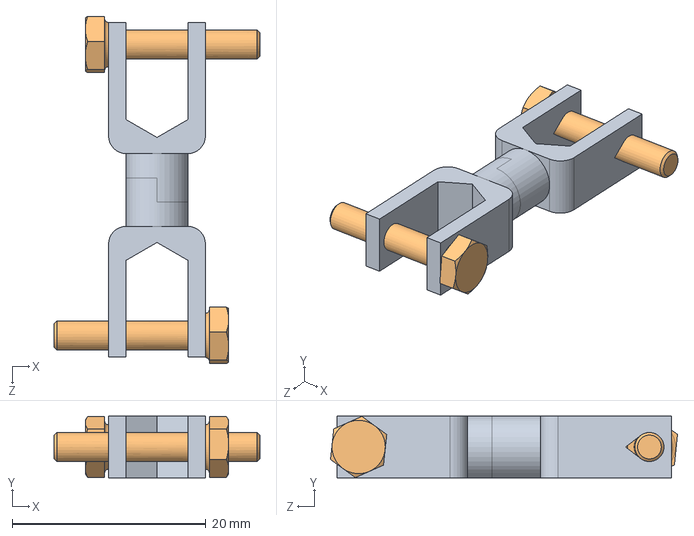
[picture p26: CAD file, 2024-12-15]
3D/EjeDeRotacion.SLDASM
21.2 x 6.35 x 35.8 mm
MedioEjeRotacion x 2
bolt_gb_t_5783_m3x16 x 2

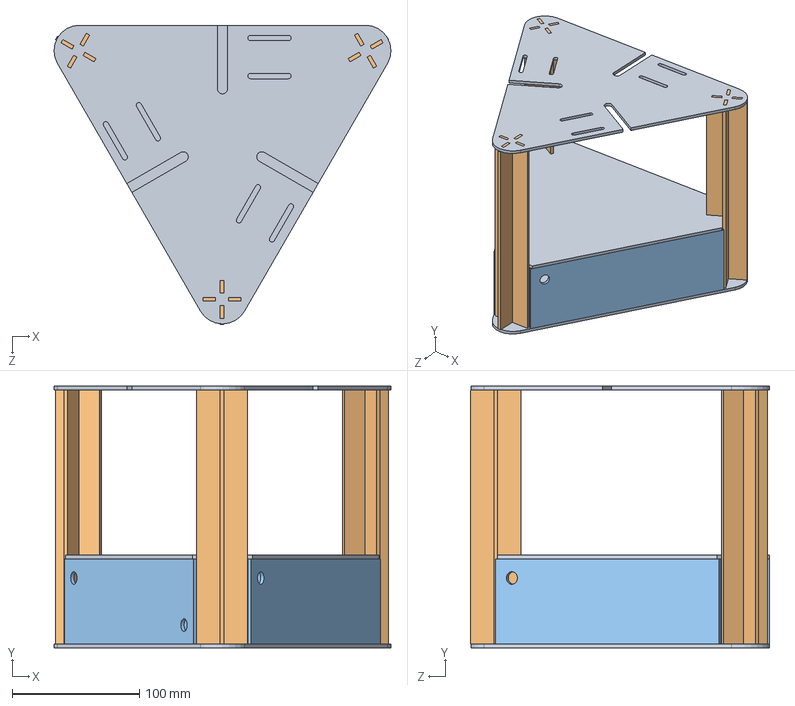
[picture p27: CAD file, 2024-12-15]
3D/Estructura Robot Delta.SLDASM
265.2 x 206.0 x 235.6 mm
Base x 3
Pata x 6
Pared x 3

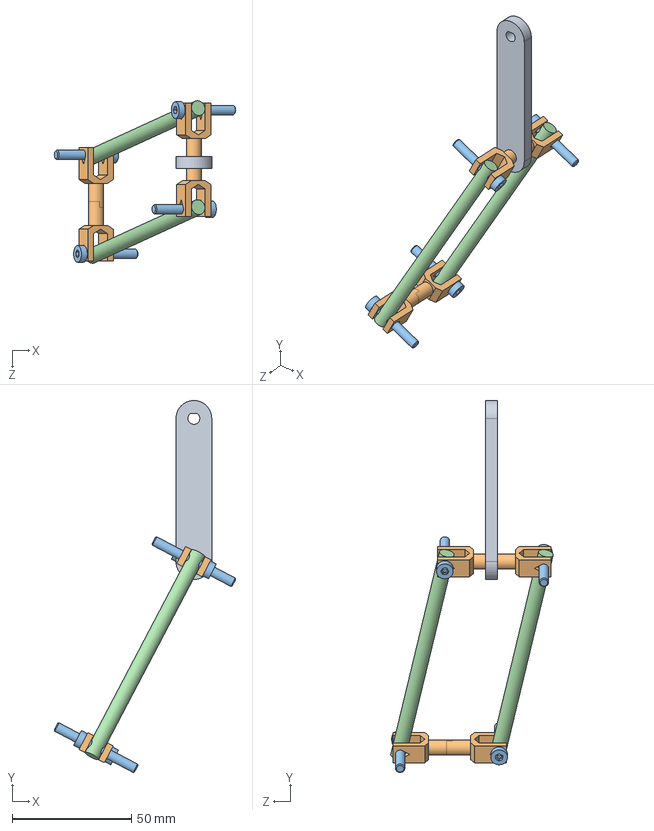
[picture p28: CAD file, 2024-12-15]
3D/Brazo.SLDASM
76.0 x 155.8 x 68.1 mm
Eslabon
MedioEjeRotacion x 4
07161-104x25 x 4
eje x 2

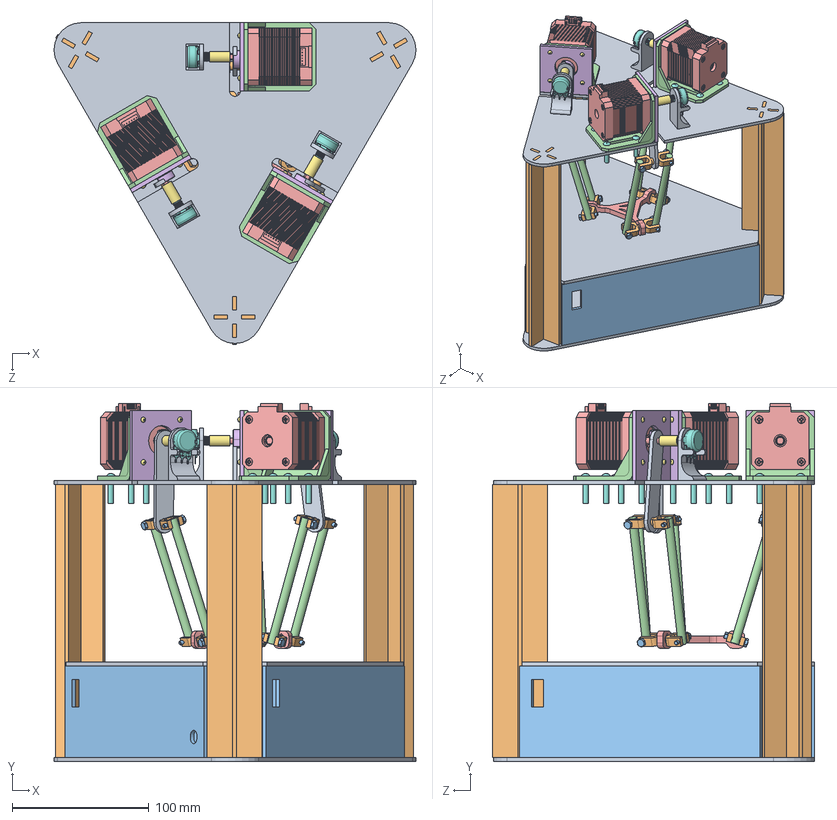
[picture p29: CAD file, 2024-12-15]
3D/Robot delta.SLDASM
265.2 x 262.3 x 235.6 mm
Base x 3
Pata x 6
Pared x 3
soporte x 3
Nema17 x 3
Cara motor x 3
M3_10mm x 12
M4_20mm x 12
Eslabon x 3
MedioEjeRotacion x 12
bolt_gb_t_5783_m3x16 x 12
eje x 6
Efector final
Seguidor_Eslabon x 3
Conector_Pot_Motor x 3
POT_WH148_15MM x 3
Base pot x 3

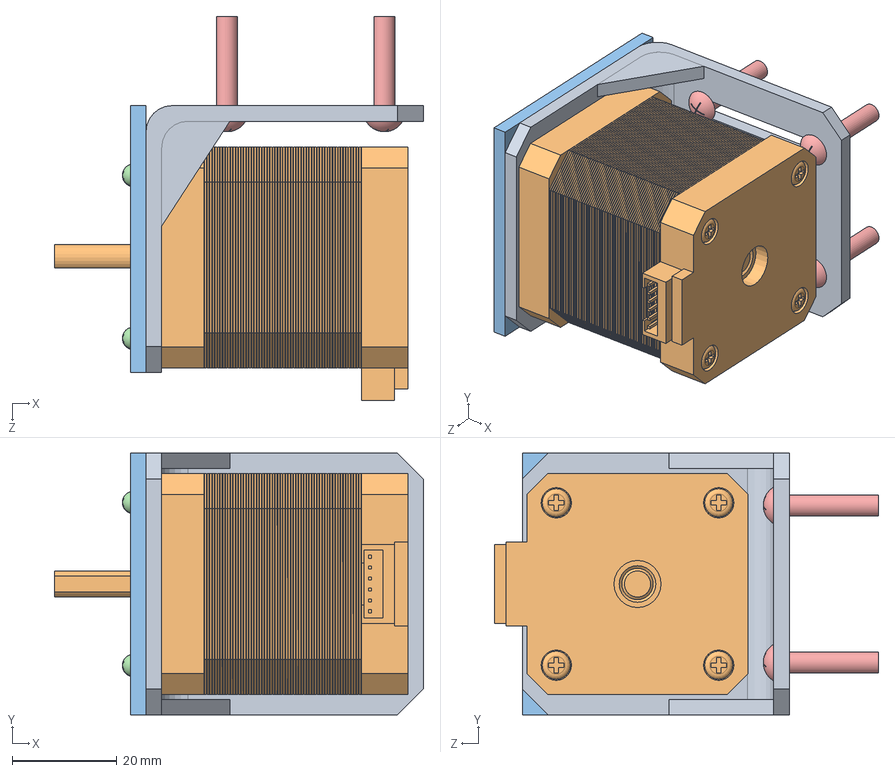
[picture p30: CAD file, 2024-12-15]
3D/Motor con base.SLDASM
70.5 x 50.0 x 73.3 mm
soporte
Nema17
Cara motor
M3_10mm x 4
M4_20mm x 4

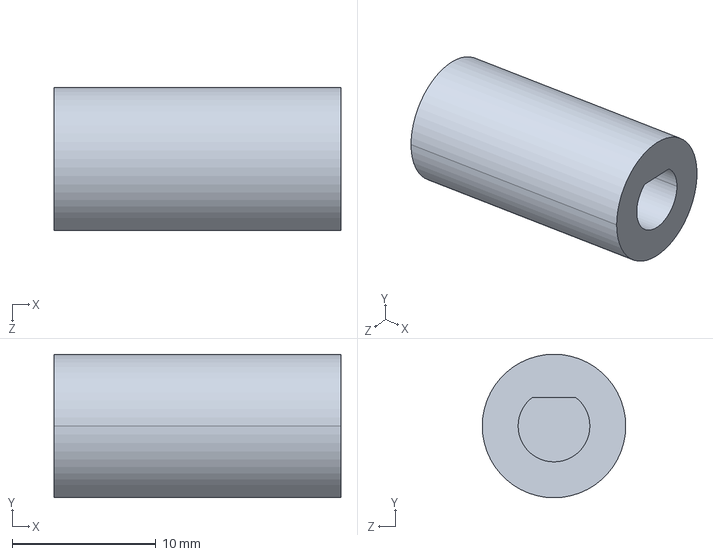
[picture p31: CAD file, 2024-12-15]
3D/Pot-motor.STEP
20.0 x 10.0 x 10.0 mm

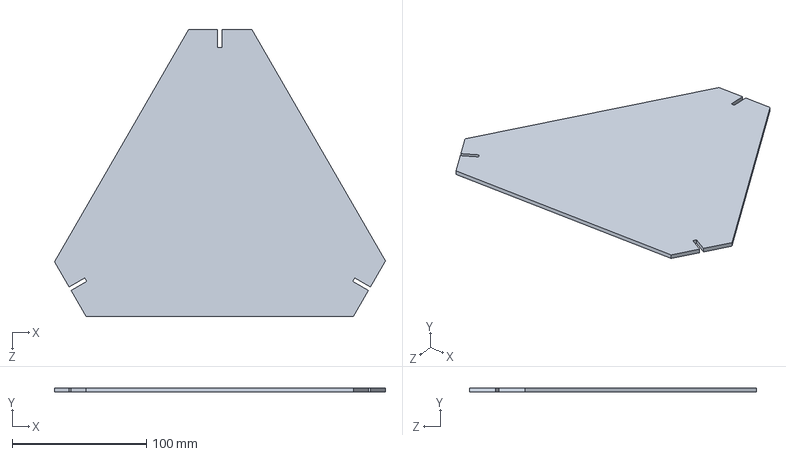
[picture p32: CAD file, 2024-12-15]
3D/Base.SLDPRT
246.9 x 3.00 x 214.1 mm

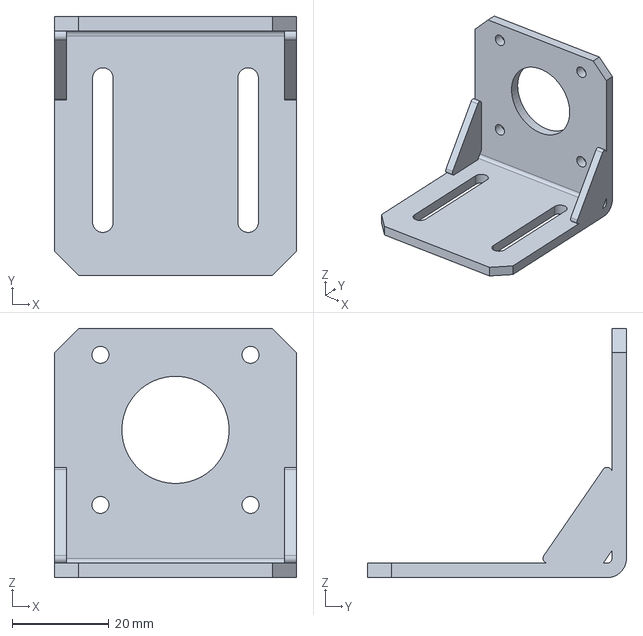
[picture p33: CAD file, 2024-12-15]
3D/NEMA 17 A-Body.step
50.0 x 53.5 x 51.5 mm

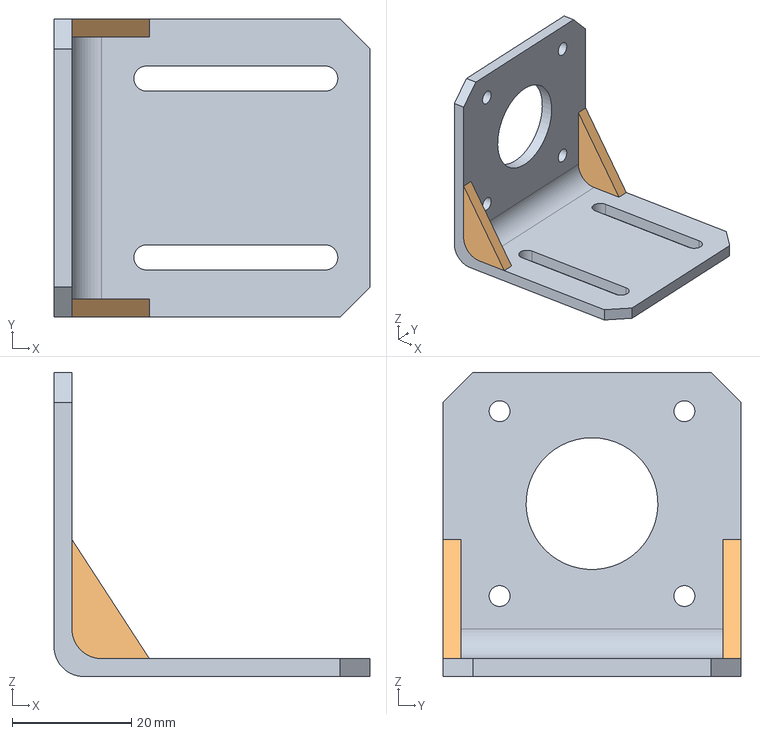
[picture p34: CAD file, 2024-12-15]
3D/nema17-mount.step
53.0 x 50.0 x 51.0 mm

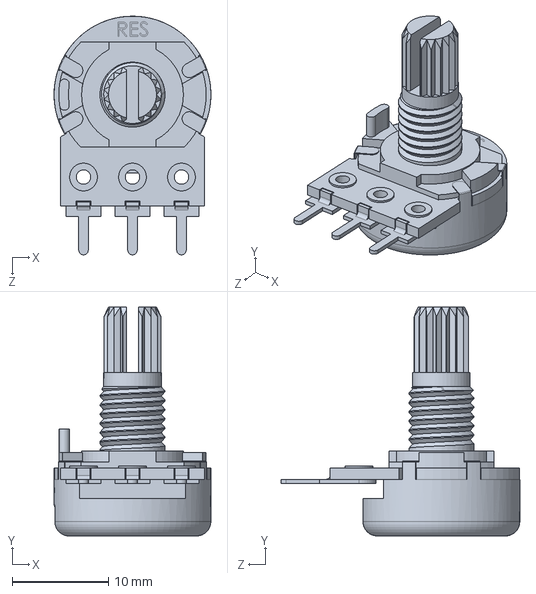
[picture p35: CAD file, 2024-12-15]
3D/POT_WH148_15MM.SLDPRT
16.3 x 23.8 x 24.9 mm

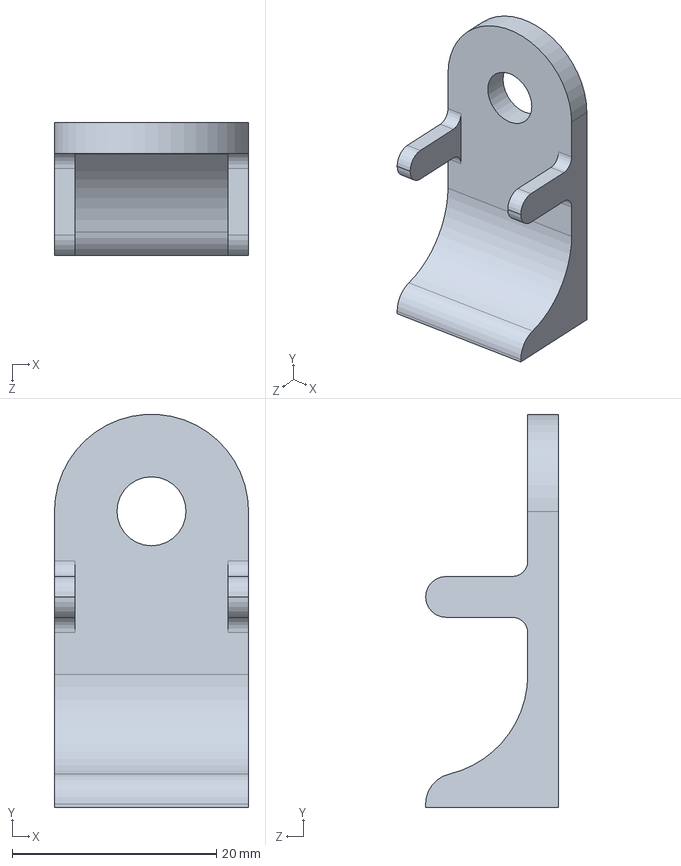
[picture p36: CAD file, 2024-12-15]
3D/Base pot.SLDPRT
19.0 x 38.5 x 13.0 mm

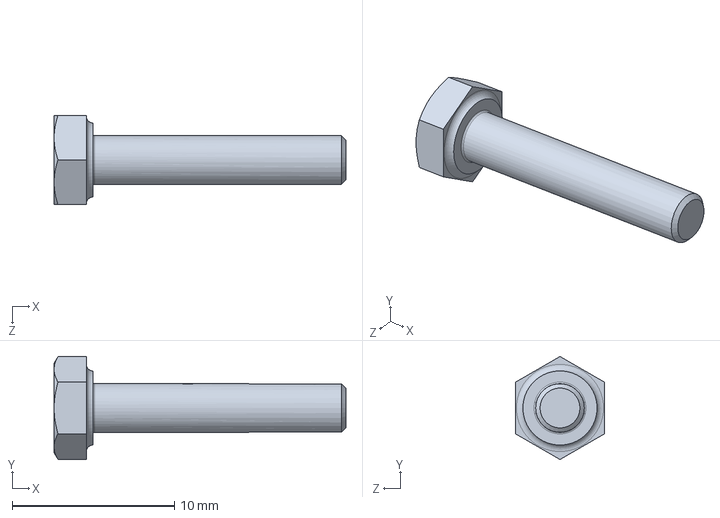
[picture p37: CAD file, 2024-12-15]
3D/Pieza3.SLDPRT
18.0 x 6.35 x 5.50 mm

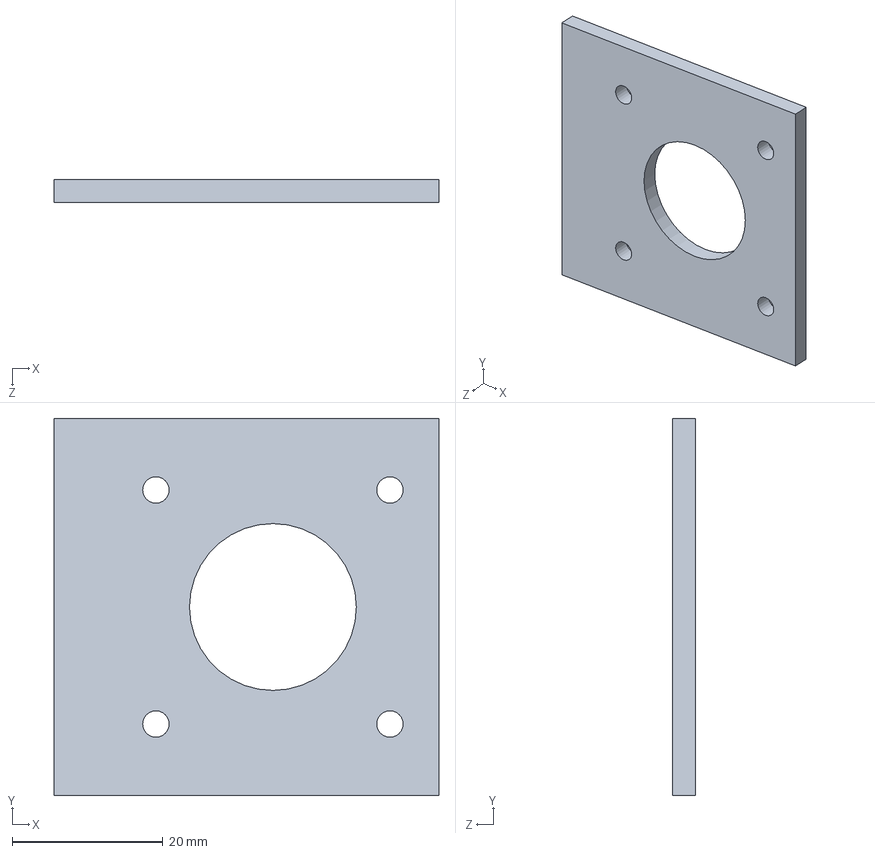
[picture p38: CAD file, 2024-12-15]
3D/Cara motor.SLDPRT
51.0 x 50.0 x 3.00 mm

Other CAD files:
3D/soporte.SLDPRT
3D/Estatorfinal.SLDPRT
3D/MedioEjeRotacion.SLDPRT
3D/vis_vth3_16pana.SLDPRT
3D/07161-104x25.SLDPRT
3D/Conector_Pot_Motor.SLDPRT
3D/Efector final.SLDPRT
3D/Eslabon.SLDPRT
3D/M3_10mm.SLDPRT
3D/M4_20mm.SLDPRT
3D/Pared.SLDPRT
3D/Pata.SLDPRT
3D/Pot-motor.SLDPRT
3D/Seguidor_Eslabon.SLDPRT
3D/bolt_gb_t_5783_m3x16.SLDPRT
3D/din6921_m5x30_8_8.SLDPRT
3D/eje.SLDPRT
3D/nema17-mount.step.SLDPRT

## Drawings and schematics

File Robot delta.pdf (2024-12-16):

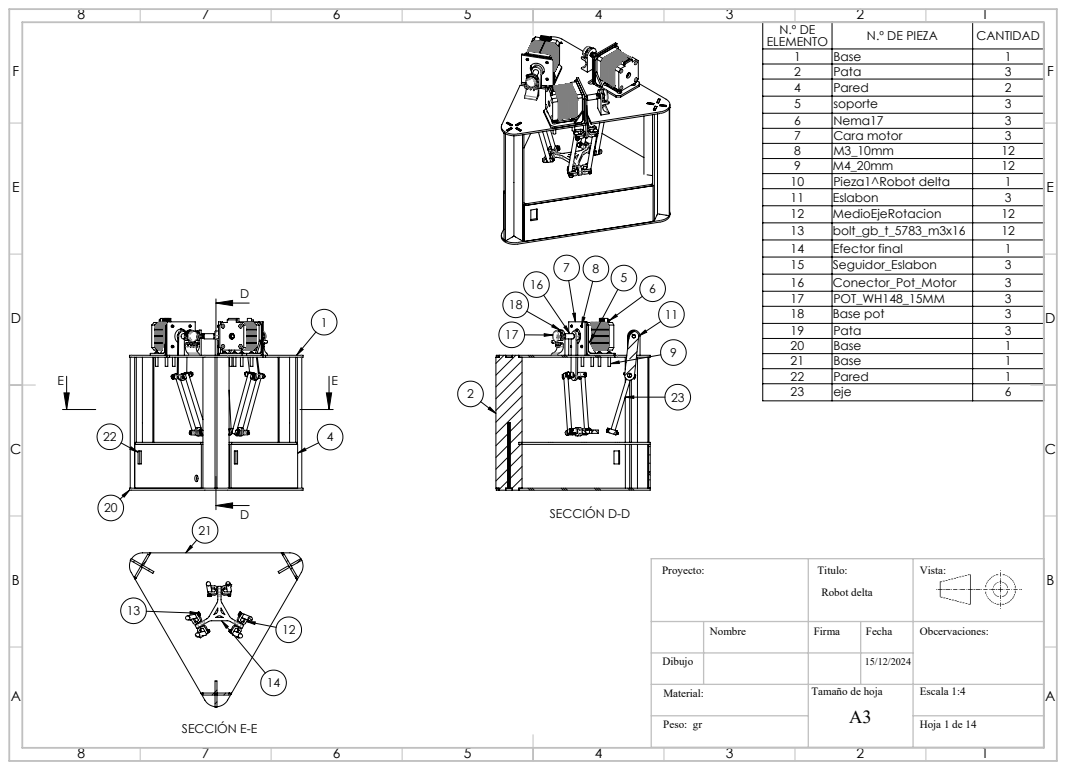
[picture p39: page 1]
SECCIÓN D-D; SECCIÓN E-E; ELEMENTO; N.º DE PIEZA; CANTIDAD 1; Base; Pata; Pared; soporte; Nema17; Cara motor; Pieza1^Robot delta; Efector final; Base pot; Peso: gr; Escala 1:4; Hoja 1 de 14; Robot delta

Tamaño de hoja

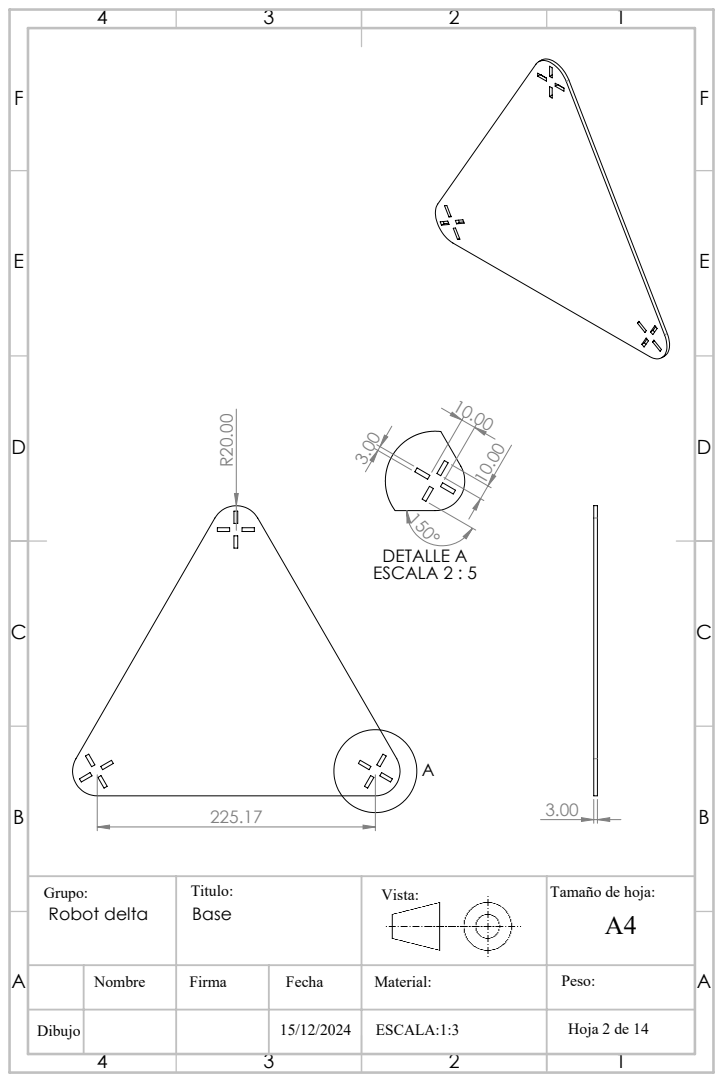
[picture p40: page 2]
DETALLE A ESCALA 2 : 5

Grupo: Robot delta | Titulo: Base | Vista: | Tamaño de hoja: A4

Nombre | Firma | Fecha | Material: | Peso:

Dibujo | | | | ESCALA:1:3

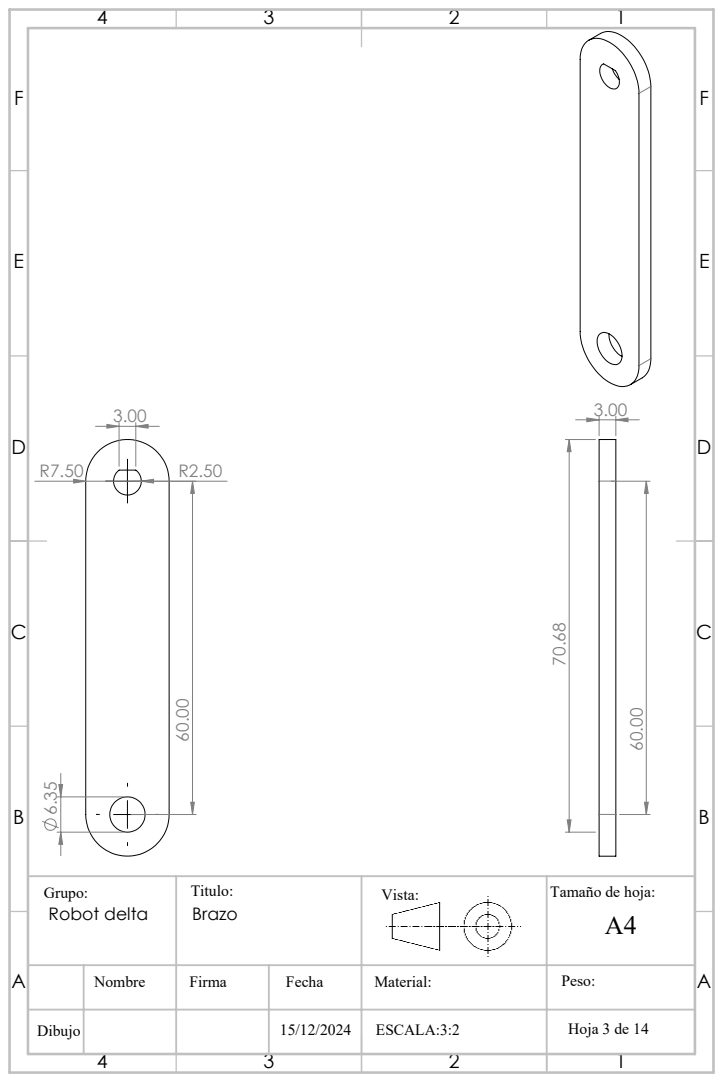
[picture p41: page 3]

Grupo: Robot delta | Titulo: Brazo | Vista: | Tamaño de hoja: A4

Nombre | Firma | Fecha | Material: | Peso:

ESCALA:3:2

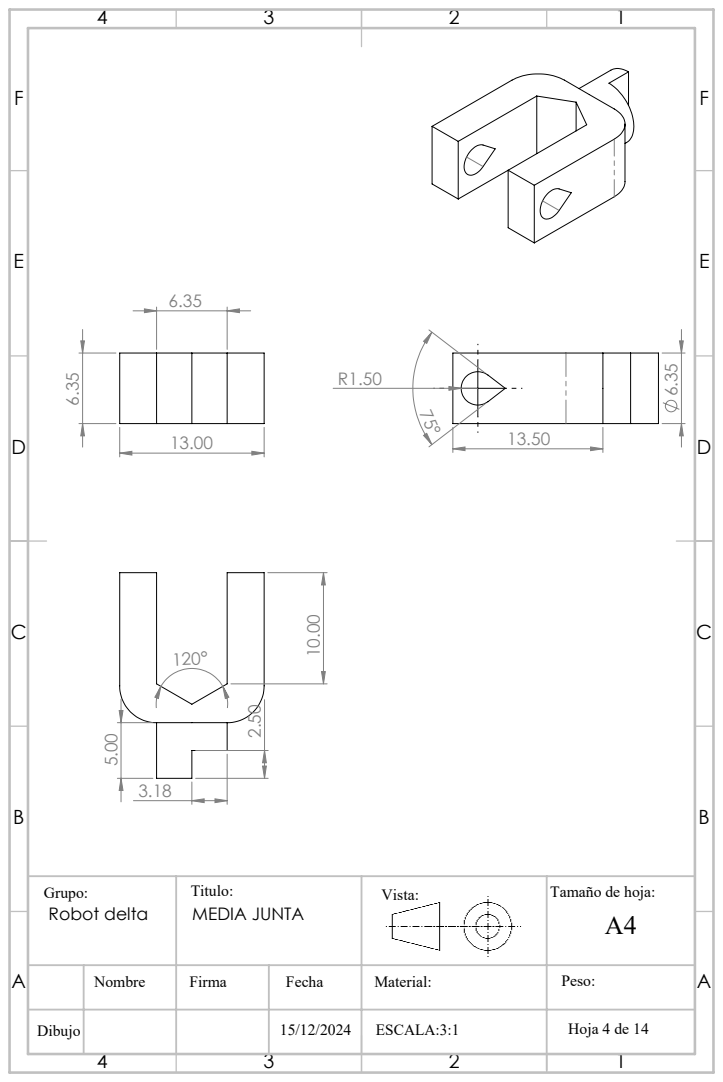
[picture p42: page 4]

Grupo: Robot delta | Titulo: MEDIA JUNTA | Vista: | Tamaño de hoja: A4

Nombre | Firma | Fecha | Material: | Peso:

ESCALA:3:1

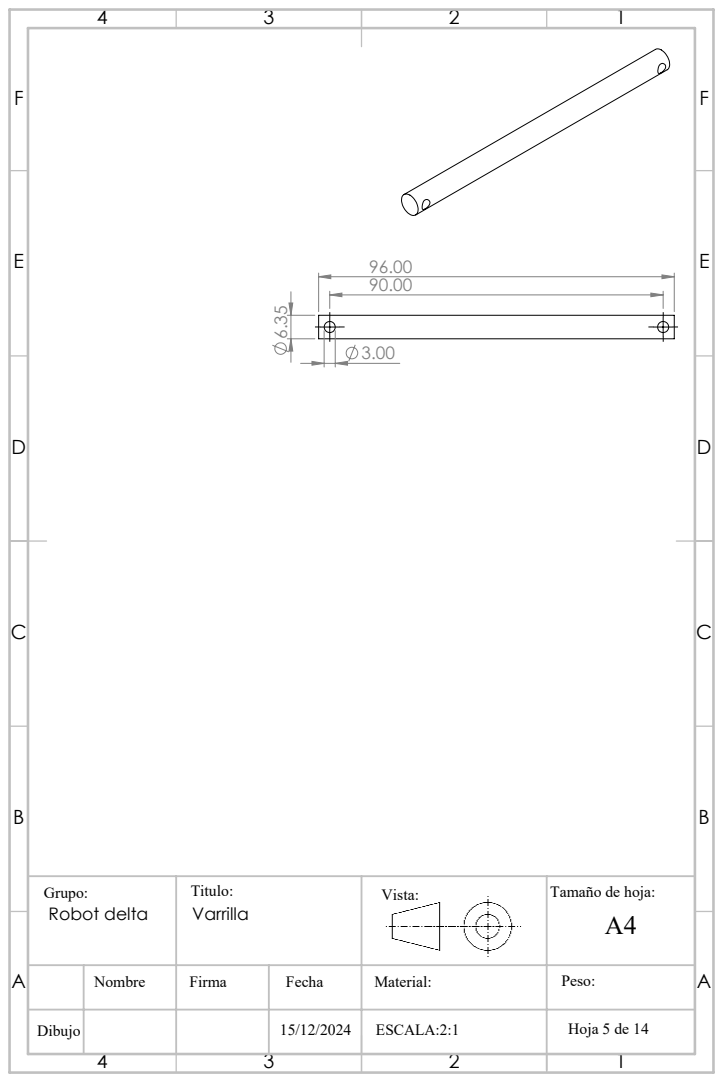
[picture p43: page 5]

Grupo: Robot delta | Titulo: Varrilla | Vista: | Tamaño de hoja: A4

Nombre | Firma | Fecha | Material: | Peso:

ESCALA:2:1

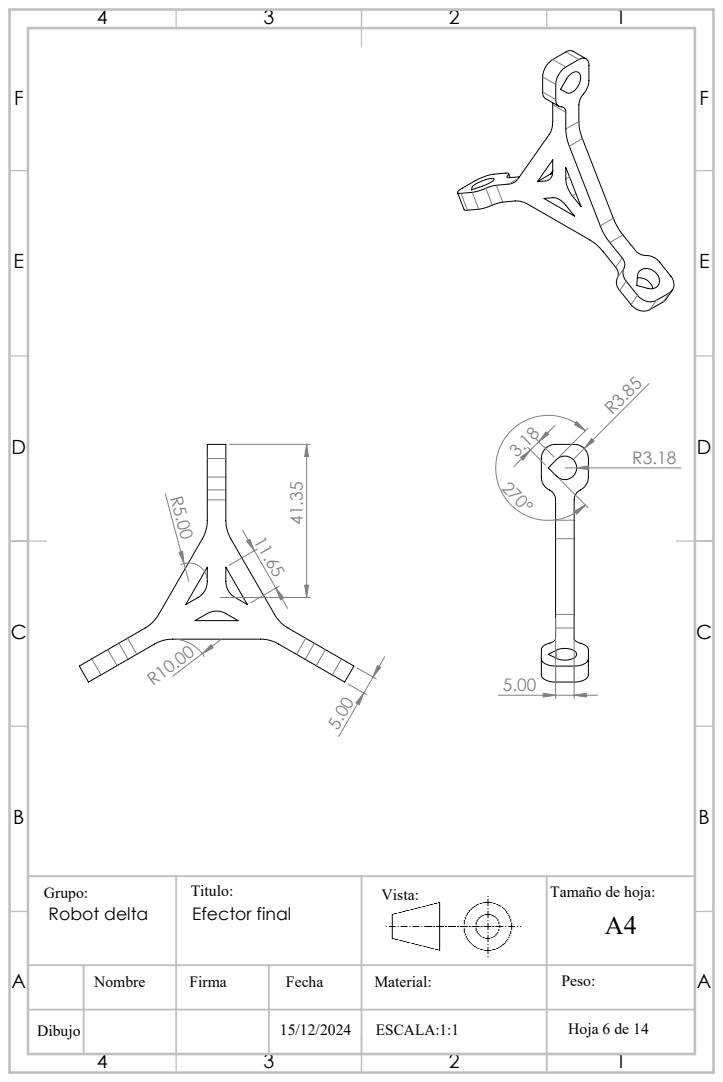
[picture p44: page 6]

Grupo: Robot delta | Titulo: Efector final | Vista: | Tamaño de hoja: A4

Nombre | Firma | Fecha | Material: | Peso:

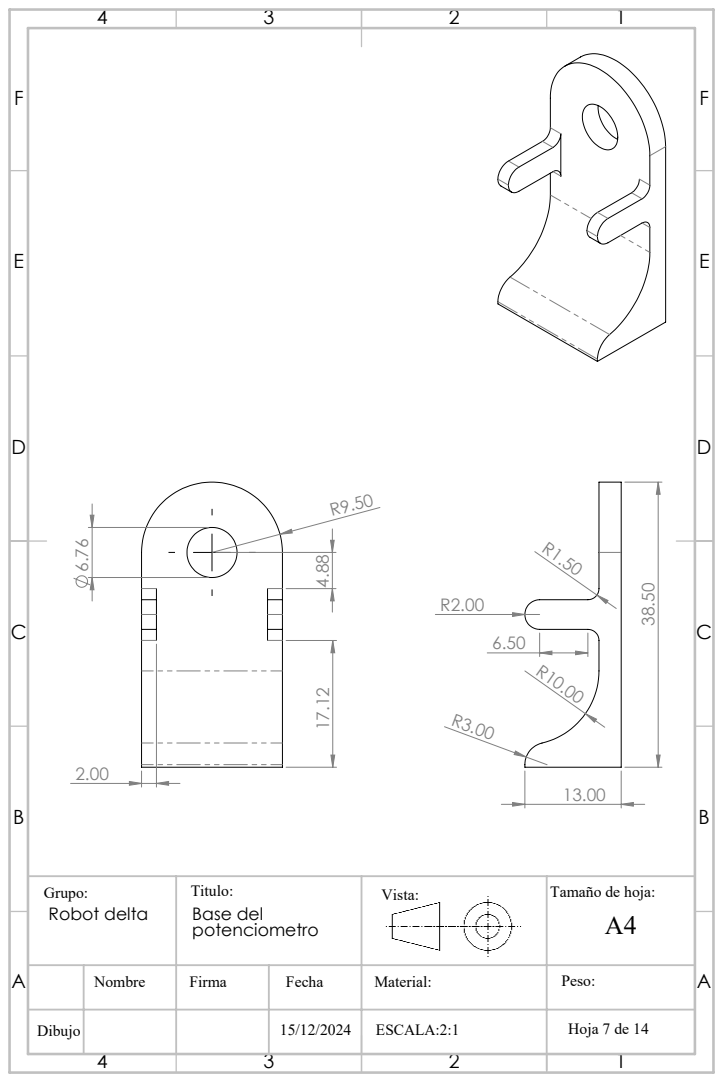
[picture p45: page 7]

Grupo: Robot delta | Titulo: Base del potenciometro | Vista: | Tamaño de hoja: A4

Nombre | Firma | Fecha | Material: | Peso:

ESCALA:2:1

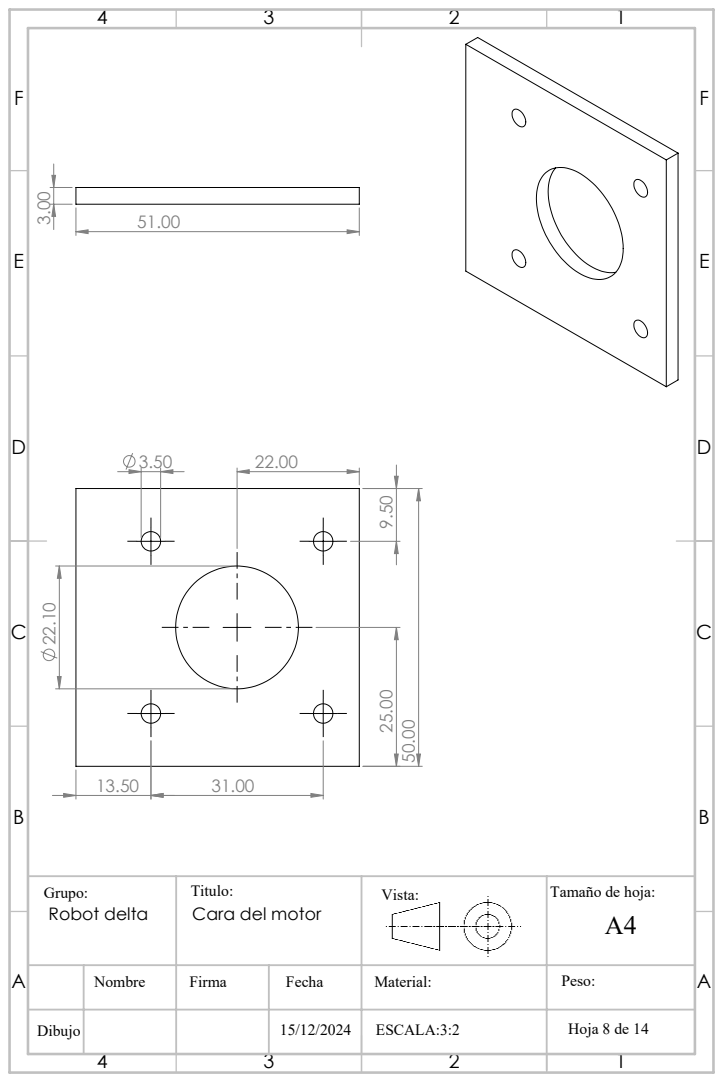
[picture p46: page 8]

Grupo: Robot delta | Titulo: Cara del motor | Vista: | Tamaño de hoja: A4

Nombre | Firma | Fecha | Material: | Peso:

ESCALA:3:2

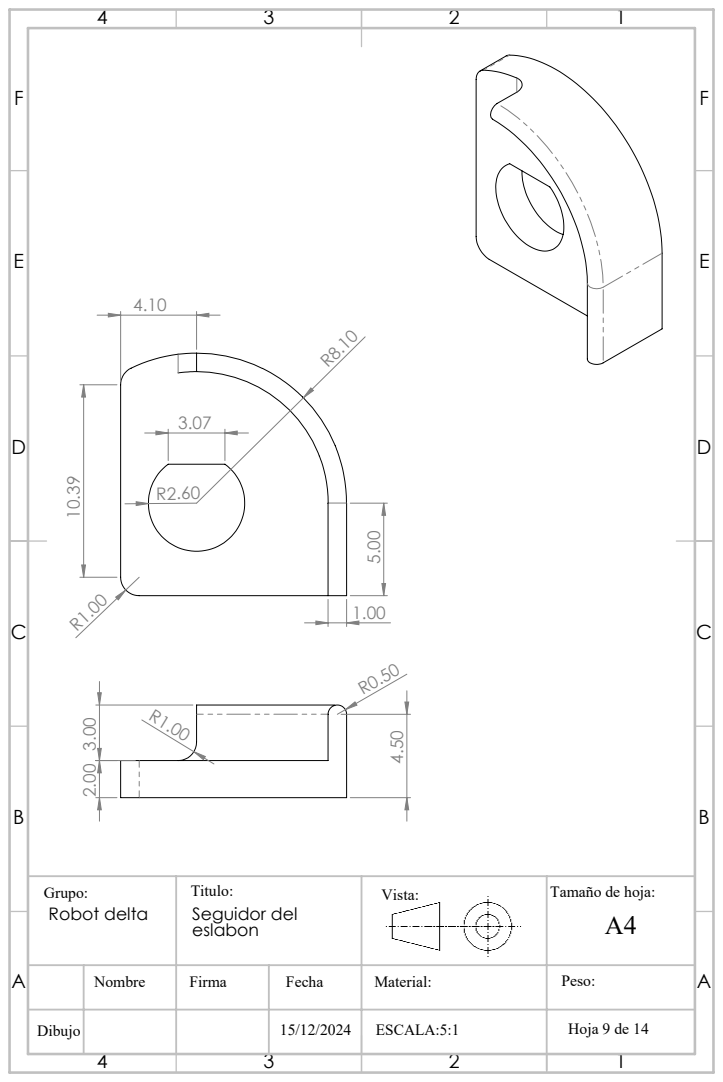
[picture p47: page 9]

Grupo: Robot delta | Titulo: Seguidor del eslabon | Vista: | Tamaño de hoja: A4

Nombre | Firma | Fecha | Material: | Peso:

ESCALA:5:1

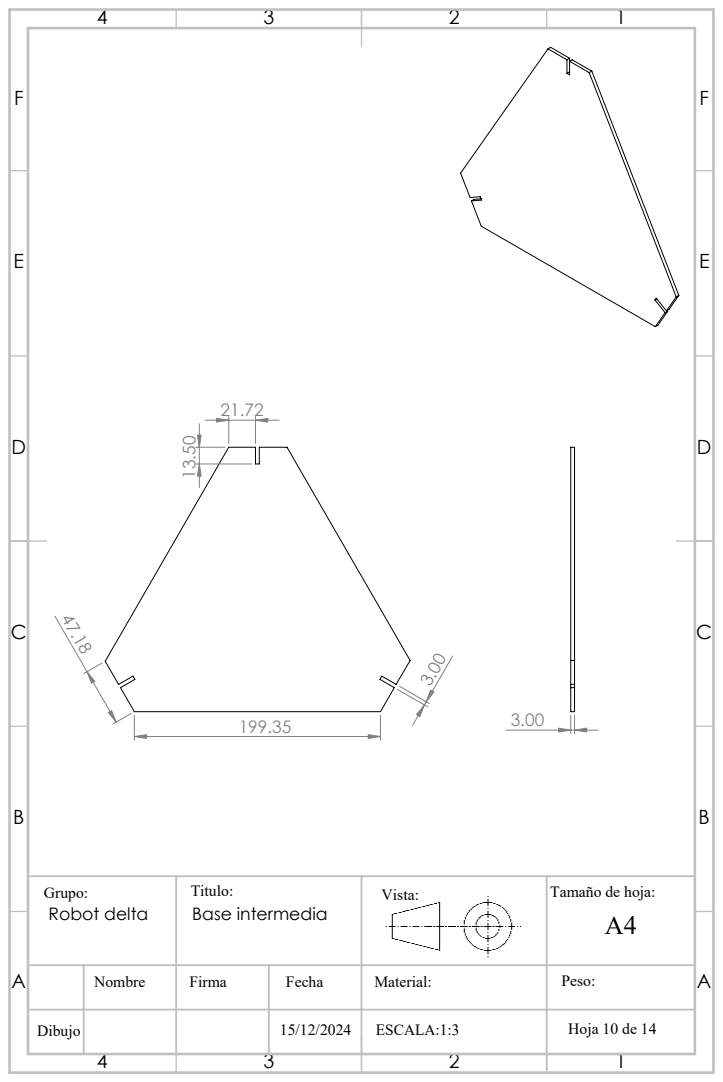
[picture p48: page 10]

Grupo: Robot delta | Titulo: Base intermedia | Vista: | Tamaño de hoja: A4

Nombre | Firma | Fecha | Material: | Peso:

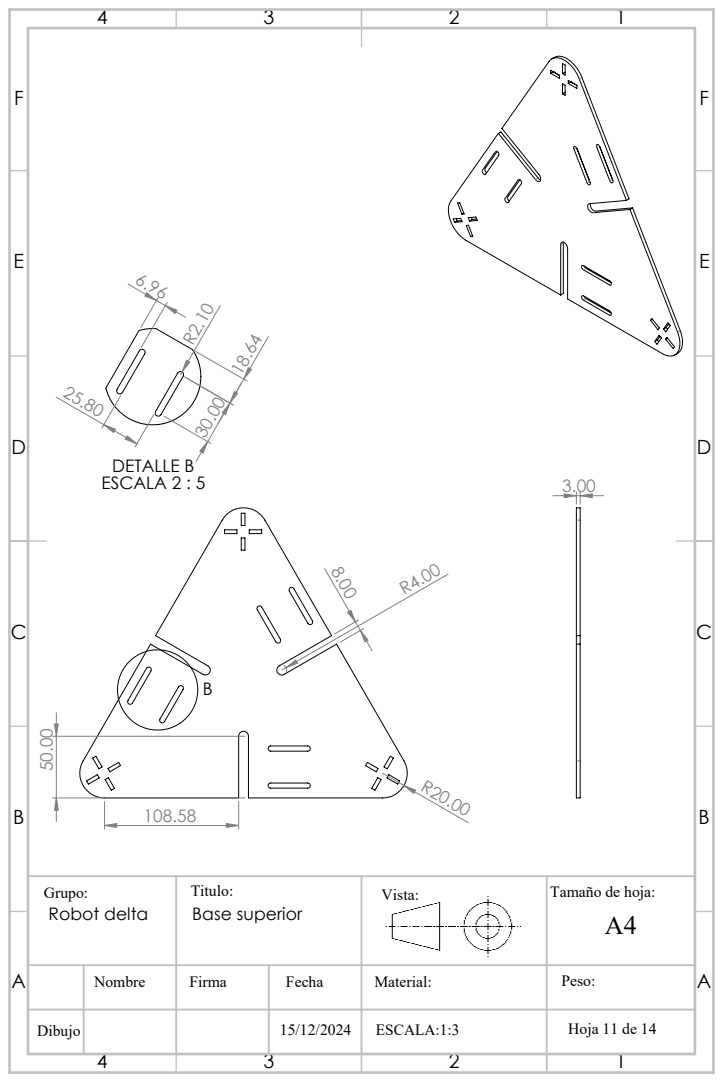
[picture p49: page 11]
DETALLE B ESCALA 2 : 5

Grupo: Robot delta | Titulo: Base superior | Vista: | Tamaño de hoja: A4

Nombre | Firma | Fecha | Material: | Peso:

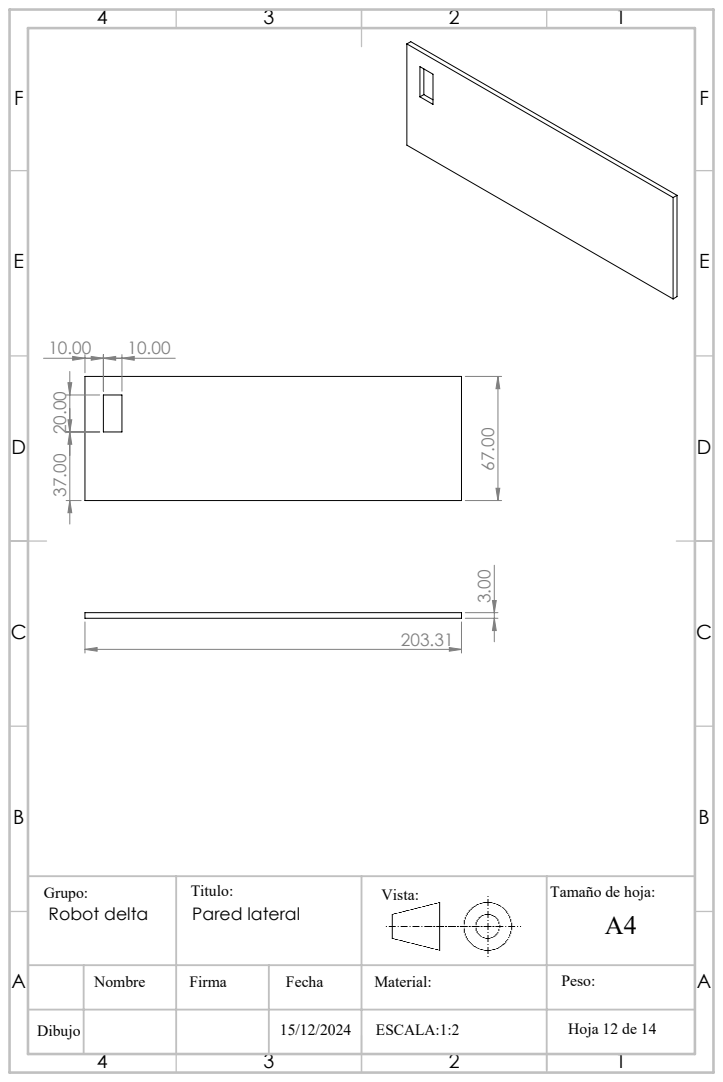
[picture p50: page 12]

Grupo: Robot delta | Titulo: Pared lateral | Vista: | Tamaño de hoja: A4

Nombre | Firma | Fecha | Material: | Peso:


Grupo: Robot delta | Titulo: Pared trasera | Vista: | Tamaño de hoja: A4

Nombre | Firma | Fecha | Material: | Peso:


Grupo: Robot delta | Titulo: Pata | Vista: | Tamaño de hoja: A4

Nombre | Firma | Fecha | Material: | Peso:

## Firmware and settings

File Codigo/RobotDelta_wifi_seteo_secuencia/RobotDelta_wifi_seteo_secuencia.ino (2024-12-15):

#include <WiFi.h>
#include <WiFiMulti.h>

// Definiciones de pines
#define paso1 15
#define dire1 2  
#define paso2 13    
#define dire2 12    
#define paso3 25   
#define dire3 26      
#define sensor_1 33
#define sensor_2 35
#define sensor_3 32

int s1, s2, s3; // Valores calculados de los sensores
int grado1;
int grado2;
int grado3;
int pasos1;
int pasos2;
int pasos3;

// Constantes del robot
int R = 60;
int r = 35;
int L1 = 60;
int L2 = 90;
int retardo = 2000;

float secuenciaX[10];
float secuenciaY[10]; 
float secuenciaZ[10]; 


WiFiMulti wifiMulti;
WiFiServer servidor(80);

// Variables globales
String modo = "cordenadas"; 
float X = 0.0, Y = 0.0, Z = -90.0; // Coordenadas cartesianas
float q1 = 50.0, q2 = 50.0, q3 = 50.0; // Ángulos de las juntas
bool bandera = false;

// Valores de seteo para 0° y 90°
int sensor1_0 = 3200, sensor1_90 = 1790;
int sensor2_0 = 3160, sensor2_90 = 1810;
int sensor3_0 = 3160, sensor3_90 = 2000;

// Declaración de funciones
void calculo_de_cordenadas();
void calculo_de_q();
void pasopaso();
void control();
void calculo_de_s();
void enviarPaginaWeb(WiFiClient &cliente);
void secuencia();

void setup() {
    // Configuración de pines como salida
    pinMode(paso1, OUTPUT);
    pinMode(dire1, OUTPUT);
    pinMode(paso2, OUTPUT);
    pinMode(dire2, OUTPUT);
    pinMode(paso3, OUTPUT);
    pinMode(dire3, OUTPUT);

    // Inicialización de la comunicación serie
    Serial.begin(115200);
    Serial.println("\nIniciando WiFi Multi");

    // Configuración de redes Wi-Fi
    wifiMulti.addAP("mazzocato", "leon6734");
    wifiMulti.addAP("MATIAS", "Emily123");
    //wifiMulti.addAP("SEBASTIAN", "12349876");

    // Configurar el modo WiFi como STA (Station)
    WiFi.mode(WIFI_STA);
    Serial.print("Conectando a WiFi...");
    while (wifiMulti.run() != WL_CONNECTED) {
        Serial.print(".");
        delay(1000); // Espera hasta que se establezca la conexión
    }

    // Validar si se obtuvo una IP válida
    if (WiFi.localIP() == INADDR_NONE || WiFi.localIP().toString() == "0.0.0.0") {
        Serial.println("\nError: No se obtuvo una IP válida. Reiniciando...");
        ESP.restart(); // Reinicia el microcontrolador
    }

    Serial.println("\nConectado a WiFi");
    Serial.print("IP local: ");
    Serial.println(WiFi.localIP());

    // Iniciar el servidor
    servidor.begin();
    Serial.println("Servidor iniciado correctamente");
}

void loop() {
    WiFiClient cliente = servidor.available();
    if (cliente) {
        Serial.println("Nuevo cliente conectado");
        String peticion = cliente.readStringUntil('\r');
        cliente.flush();

        // Cambiar entre modos según la solicitud
        if (peticion.indexOf("GET /modo/cordenadas") >= 0) {
            modo = "cordenadas";
        } else if (peticion.indexOf("GET /modo/joins") >= 0) {
            modo = "joins";
        } else if (peticion.indexOf("GET /modo/seteo") >= 0) {
            modo = "seteo";
        } else if (peticion.indexOf("GET /modo/secuencia") >= 0) {
            modo = "secuencia";
        }  else if (peticion.indexOf("GET /guardar?sensor=") >= 0) {
    // Extraer parámetros de la solicitud
    int sensorIndex = peticion.indexOf("sensor=");
    int posicionIndex = peticion.indexOf("posicion=");

    String sensor = peticion.substring(sensorIndex + 7, peticion.indexOf('&', sensorIndex));
    String posicion = peticion.substring(posicionIndex + 9);

    int valor = 0;

    if (sensor == "1") {
        valor = analogRead(sensor_1);
        if (posicion == "0") sensor1_0 = valor;
        else if (posicion == "90") sensor1_90 = valor;
    } else if (sensor == "2") {
        valor = analogRead(sensor_2);
        if (posicion == "0") sensor2_0 = valor;
        else if (posicion == "90") sensor2_90 = valor;
    } else if (sensor == "3") {
        valor = analogRead(sensor_3);
        if (posicion == "0") sensor3_0 = valor;
        else if (posicion == "90") sensor3_90 = valor;
    }

    // Enviar una respuesta simple
    cliente.println("HTTP/1.1 200 OK");
    cliente.println("Content-Type: text/plain");
    cliente.println("Connection: close");
    cliente.println();
    cliente.println("OK");

    Serial.println("Valor guardado correctamente");
        } else if (peticion.startsWith("GET /actualizar?")) {

            // Extraer parámetros de la solicitud
            int q1Index = peticion.indexOf("q1=");
            int q2Index = peticion.indexOf("q2=");
            int q3Index = peticion.indexOf("q3=");
            int xIndex = peticion.indexOf("X=");
            int yIndex = peticion.indexOf("Y=");
            int zIndex = peticion.indexOf("Z=");
            int s1_0Index = peticion.indexOf("sensor1_0=");
            int s1_90Index = peticion.indexOf("sensor1_90=");
            int s2_0Index = peticion.indexOf("sensor2_0=");
            int s2_90Index = peticion.indexOf("sensor2_90=");
            int s3_0Index = peticion.indexOf("sensor3_0=");
            int s3_90Index = peticion.indexOf("sensor3_90=");

            if (q1Index >= 0) q1 = peticion.substring(q1Index + 3, peticion.indexOf('&', q1Index)).toFloat();
            if (q2Index >= 0) q2 = peticion.substring(q2Index + 3, peticion.indexOf('&', q2Index)).toFloat();
            if (q3Index >= 0) q3 = peticion.substring(q3Index + 3, peticion.indexOf('&', q3Index)).toFloat();
            if (xIndex >= 0) X = peticion.substring(xIndex + 2, peticion.indexOf('&', xIndex)).toFloat();
            if (yIndex >= 0) Y = peticion.substring(yIndex + 2, peticion.indexOf('&', yIndex)).toFloat();
            if (zIndex >= 0) Z = peticion.substring(zIndex + 2, peticion.indexOf('&', zIndex)).toFloat();
            bandera = false;
        }

        // Enviar la página web al cliente
        enviarPaginaWeb(cliente);

        // Control según el modo seleccionado
        if (!bandera) {
            calculo_de_s();
            control();
            bandera = true;
        }

        cliente.stop();
        Serial.println("Cliente desconectado");
    }
}

void enviarPaginaWeb(WiFiClient &cliente) {
    // Encabezados HTTP
    cliente.println("HTTP/1.1 200 OK");
    cliente.println("Content-Type: text/html; charset=UTF-8");
    cliente.println("Connection: close");
    cliente.println();

    // Página web
    cliente.println("<!DOCTYPE HTML>");
    cliente.println("<html>");
    cliente.println("<head>");
    cliente.println("<style>");
    cliente.println("button { background-color: #4CAF50; color: white; padding: 10px; margin: 5px; }");
    cliente.println("input { width: 50px; }");
    cliente.println("</style>");
    cliente.println("</head>");
    cliente.println("<body>");

    // Botones para cambiar de modo
    cliente.println("<button onclick=\"location.href='/modo/seteo'\">Modo: Seteo</button>");
    cliente.println("<button onclick=\"location.href='/modo/cordenadas'\">Modo: Coordenadas</button>");
    cliente.println("<button onclick=\"location.href='/modo/joins'\">Modo: Joins</button>");
    cliente.println("<button onclick=\"location.href='/modo/secuencia'\">Modo: Secuencia</button>");

    // Mostrar campos según el modo
    if (modo == "cordenadas") {
        cliente.println("<h2>Modo: Coordenadas</h2>");
        cliente.printf("<p>X=<input type='text' id='X' value='%.2f'></p>", X);
        cliente.printf("<p>Y=<input type='text' id='Y' value='%.2f'></p>", Y);
        cliente.printf("<p>Z=<input type='text' id='Z' value='%.2f'></p>", Z);
        cliente.printf("<p>q1=%.2f</p>", q1);
        cliente.printf("<p>q2=%.2f</p>", q2);
        cliente.printf("<p>q3=%.2f</p>", q3);
    } else if (modo == "joins") {
        cliente.println("<h2>Modo: Joins</h2>");
        cliente.printf("<p>q1=<input type='text' id='q1' value='%.2f'></p>", q1);
        cliente.printf("<p>q2=<input type='text' id='q2' value='%.2f'></p>", q2);
        cliente.printf("<p>q3=<input type='text' id='q3' value='%.2f'></p>", q3);
        cliente.printf("<p>S1=%.2f</p>", s1);
        cliente.printf("<p>S2=%.2f</p>", s2);
        cliente.printf("<p>S3=%.2f</p>", s3);
    } else if (modo == "seteo") {
        cliente.println("<h3>Seteo de Sensores</h3>");

        // Sensor 1
        cliente.println("<div>");
        cliente.printf("<p>Sensor 1 = <strong>%d</strong></p>", analogRead(sensor_1));
        cliente.println("<button onclick=\"guardarSensor(1, '0')\">0°</button>");
        cliente.println("<button onclick=\"guardarSensor(1, '90')\">90°</button>");
        cliente.printf("<p>S1 = %d &nbsp;&nbsp; 0° = <strong>%d</strong> &nbsp;&nbsp; 90° = <strong>%d</strong></p>", 
                       s1, sensor1_0, sensor1_90);
        cliente.println("</div>");

        // Sensor 2
        cliente.println("<div>");
        cliente.printf("<p>Sensor 2 = <strong>%d</strong></p>", analogRead(sensor_2));
        cliente.println("<button onclick=\"guardarSensor(2, '0')\">0°</button>");
        cliente.println("<button onclick=\"guardarSensor(2, '90')\">90°</button>");
        cliente.printf("<p>S2 = %d &nbsp;&nbsp; 0° = <strong>%d</strong> &nbsp;&nbsp; 90° = <strong>%d</strong></p>", 
                       s2, sensor2_0, sensor2_90);
        cliente.println("</div>");

        // Sensor 3
        cliente.println("<div>");
        cliente.printf("<p>Sensor 3 = <strong>%d</strong></p>", analogRead(sensor_3));
        cliente.println("<button onclick=\"guardarSensor(3, '0')\">0°</button>");
        cliente.println("<button onclick=\"guardarSensor(3, '90')\">90°</button>");
        cliente.printf("<p>S3 = %d &nbsp;&nbsp; 0° = <strong>%d</strong> &nbsp;&nbsp; 90° = <strong>%d</strong></p>", 
                       s3, sensor3_0, sensor3_90);
        cliente.println("</div>");

        // JavaScript para guardar valores
        cliente.println("<script>");
        cliente.println("function guardarSensor(sensor, posicion) {");
        cliente.println("  fetch(`/guardar?sensor=` + sensor + `&posicion=` + posicion)");
        cliente.println("    .then(response => {");
        cliente.println("      if (response.ok) {");
        cliente.println("        alert(`Valor guardado: Sensor ${sensor} en ${posicion}°.`);");
        cliente.println("        location.reload();");
        cliente.println("      } else {");
        cliente.println("        alert('Error al guardar el valor del sensor.');");
        cliente.println("      }");
        cliente.println("    });");
        cliente.println("}");
        cliente.println("</script>");
    } else if (modo == "secuencia") {
        cliente.println("<h2>Modo: Secuencia</h2>");
        cliente.println("<form>");
        cliente.println("<table>");
        cliente.println("<tr><th>Paso</th><th>X</th><th>Y</th><th>Z</th></tr>");
        for (int i = 0; i < 10; i++) {
            cliente.println("<tr>");
            cliente.printf("<td>%d</td>", i + 1);
            cliente.printf("<td><input type='text' id='X%d' value='%.2f'></td>", i, secuenciaX[i]);
            cliente.printf("<td><input type='text' id='Y%d' value='%.2f'></td>", i, secuenciaY[i]);
            cliente.printf("<td><input type='text' id='Z%d' value='%.2f'></td>", i, secuenciaZ[i]);
            cliente.println("</tr>");
        }
        cliente.println("</table>");
        cliente.println("<button type='button' onclick='actualizarSecuencia()'>Guardar Secuencia</button>");
        cliente.println("</form>");
    }

    // Botón de actualizar (excepto en modo seteo)
    if (modo != "seteo") {
        cliente.println("<button onclick=\"actualizar()\">Actualizar</button>");
    }

    // JavaScript para Actualizar
    cliente.println("<script>");
    cliente.println("function actualizar() {");
    cliente.println("  let params = '';");

    if (modo == "cordenadas") {
        cliente.println("  params += 'X=' + document.getElementById('X').value + '&';");
        cliente.println("  params += 'Y=' + document.getElementById('Y').value + '&';");
        cliente.println("  params += 'Z=' + document.getElementById('Z').value;");
    } else if (modo == "joins") {
        cliente.println("  params += 'q1=' + document.getElementById('q1').value + '&';");
        cliente.println("  params += 'q2=' + document.getElementById('q2').value + '&';");
        cliente.println("  params += 'q3=' + document.getElementById('q3').value;");
    }
    cliente.println("  fetch('/actualizar?' + params).then(response => location.reload());");
    cliente.println("}");
    cliente.println("</script>");

    cliente.println("</body>");
    cliente.println("</html>");
}


void control() {
    if (modo == "cordenadas") {
        calculo_de_q();
        pasopaso();
    } else if (modo == "joins") {
        //calculo_de_cordenadas();
        pasopaso();
    } else if (modo == "secuencia"){
        //secuencia();
    }
}

void calculo_de_q() {
  float a1 = -2*Z*L1;
  float b1 = 2*L1*(X*cos(0)+Y*sin(0)+r-R);
  float c1 = pow(X+cos(0)*(r-R),2)+pow(Y+sin(0)*(r-R),2)+pow(Z,2)+pow(L1,2)-pow(L2,2);

  float a2 = -2*Z*L1;
  float b2 = 2*L1*(X*cos(radians(120))+Y*sin(radians(120))+r-R);
  float c2 = pow(X+cos(radians(120))*(r-R),2)+pow(Y+sin(radians(120))*(r-R),2)+pow(Z,2)+pow(L1,2)-pow(L2,2);

  float a3 = -2*Z*L1;
  float b3 = 2*L1*(X*cos(radians(240))+Y*sin(radians(240))+r-R);
  float c3 = pow(X+cos(radians(240))*(r-R),2)+pow(Y+sin(radians(240))*(r-R),2)+pow(Z,2)+pow(L1,2)-pow(L2,2);

  float q1rad = asin(c1/sqrt(pow(a1,2)+pow(b1,2)))-atan(b1/a1);
  float q2rad = asin(c2/sqrt(pow(a2,2)+pow(b2,2)))-atan(b2/a2);
  float q3rad = asin(c3/sqrt(pow(a3,2)+pow(b3,2)))-atan(b3/a3);

  q1 = (int)(q1rad*(180/PI));
  q2 = (int)(q2rad*(180/PI));
  q3 = (int)(q3rad*(180/PI));
}

void pasopaso() {
  pasos1 = floor((abs(q1-grado1)/1.8)*16);
  pasos2 = floor((abs(q2-grado2)/1.8)*16);
  pasos3 = floor((abs(q3-grado3)/1.8)*16);

  Serial.print("pasos1: "); Serial.print(pasos1);
  Serial.print(" pasos2: "); Serial.print(pasos2);
  Serial.print(" pasos3: "); Serial.println(pasos3);

  if(q1>grado1 && q1>=0 && q1<=90 && q2>=0 && q2<=90 && q3>=0 && q3<=90){
    digitalWrite(dire1, HIGH);   // direccion de giro 0
    for(int i1=0; i1<=pasos1; i1++){
      digitalWrite(paso1, HIGH);      
      delayMicroseconds(retardo);          
      digitalWrite(paso1, LOW);       
      delayMicroseconds(retardo);
    }
  }
  if(q2>grado2 && q1>=0 && q1<=90 && q2>=0 && q2<=90 && q3>=0 && q3<=90){
    digitalWrite(dire2, HIGH);   // direccion de giro 0
    for(int i2=0; i2<=pasos2; i2++){
      digitalWrite(paso2, HIGH);      
      delayMicroseconds(retardo);          
      digitalWrite(paso2, LOW);       
      delayMicroseconds(retardo);
    }
  }
  if(q3>grado3 && q1>=0 && q1<=90 && q2>=0 && q2<=90 && q3>=0 && q3<=90){
    digitalWrite(dire3, HIGH);   // direccion de giro 0
    for(int i3=0; i3<=pasos3; i3++){
      //Serial.println("Direccion giro 1");
      digitalWrite(paso3, HIGH);      
      delayMicroseconds(retardo);          
      digitalWrite(paso3, LOW);       
      delayMicroseconds(retardo);
    }
  }
  if(q1<grado1 && q1>=0 && q1<=90 && q2>=0 && q2<=90 && q3>=0 && q3<=90){
    digitalWrite(dire1, LOW);   // direccion de giro 0
    for(int j1=0; j1<=pasos1; j1++){
      digitalWrite(paso1, HIGH);      
      delayMicroseconds(retardo);          
      digitalWrite(paso1, LOW);       
      delayMicroseconds(retardo);
    }
  }
  if(q2<grado2 && q1>=0 && q1<=90 && q2>=0 && q2<=90 && q3>=0 && q3<=90){
    digitalWrite(dire2, LOW);   // direccion de giro 0
    for(int j2=0; j2<=pasos2; j2++){
      digitalWrite(paso2, HIGH);      
      delayMicroseconds(retardo);          
      digitalWrite(paso2, LOW);       
      delayMicroseconds(retardo);
    }
  }
  if(q3<grado3 && q1>=0 && q1<=90 && q2>=0 && q2<=90 && q3>=0 && q3<=90){
    digitalWrite(dire3, LOW);   // direccion de giro 0
    for(int j3=0; j3<=pasos3; j3++){
      //Serial.println("Direccion giro 2");
      digitalWrite(paso3, HIGH);      
      delayMicroseconds(retardo);          
      digitalWrite(paso3, LOW);       
      delayMicroseconds(retardo);
    }
  }
  Serial.print("s1: "); Serial.print(s1);
  Serial.print(" s2: "); Serial.print(s2);
  Serial.print(" s3: "); Serial.println(s3);
}

void calculo_de_s() {
  grado1 = map(s1, 3200, 1790, 0, 90);
  grado2 = map(s2, 3160, 1810, 0, 90);
  grado3 = map(s3, 3160, 2000, 0, 90);

  Serial.print("s1: "); Serial.print(grado1);
  Serial.print(" s2: "); Serial.print(grado2);
  Serial.print(" s3: "); Serial.println(grado3);
}

void secuencia() {
  for (int i = 0; i < 10; i++) {
    // Actualizar coordenadas para este paso
    X = secuenciaX[i];
    Y = secuenciaY[i];
    Z = secuenciaZ[i];

    // Calcular ángulos y mover motores
    calculo_de_q();
    pasopaso();

    // Agregar un retardo opcional entre pasos
    delay(1000);
  }
}
